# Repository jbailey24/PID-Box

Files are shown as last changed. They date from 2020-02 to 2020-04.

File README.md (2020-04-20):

# PID BOX
### By Julia and Mekhi

<General description of box with photos>
	
Isometric view of boxPID box side viewPID box running

## Initial Planning
 
Digital sketchSketch

The first thing we did when confronted by this new project, is pull out pencils and paper (well, also iPad and stylus). While our initial sketches stayed fairly close to our final product, there were a few major differences, the most notable of which being the shape change. We found that in the end that having it be a cube was better for optimizing space usage. Another thing we changed was the position of the photointerrupter. Originally we had it level with the motor, but because of the shape change, we placed it below the motor in the final design.

## Schedule

| _Week_ | _Goal_ |
|---|---|
| 11/18-11/22| Make schedule and CAD/code foundation |
| 11/25-11/26 | Make RPM code |
| 12/2-12/6 | Make 3D printed parts in CAD and PID Code|
| 12/9-12/13 | Finish CAD model and RGB code |
| 12/16 | Finalize Code, 3D print motor brackets, and laser cut sides |
| 1/6-1/10 | Assemble box |
| 1/13-1/16 | Add code, test, fix errors, repeat |
| 1/20-1/24 | Add code, test, fix errors, repeat |
| 1/27-1/31 | Add code, test, fix errors, repeat |
| 2/3-2/7 | Finish |

## Materials

* Acrylic
* Screws and nuts
* 3D printer
* Arduino Uno
* Breadboard
* Wires
* 6 AA batteries in battery case
* Solder and soldering iron
* DC Motor
* Photointerrupter
* LCD and backpack
* Toggle switch
* LED
* Potentiometer
* RGB LED
* Standoffs
* Washers

## Steps

* Come up with a rough plan and schedule 
* Design PID box in SolidWorks
* 3D print motor bracket
* Laser cut the sides and wheel
* Assemble box
* Wire box
* Write and upload code
* Test and perfect code
* Done!

## CAD
  
Isometric view of CADView of inside of CAD

For this project, we used SolidWorks as our CAD platform. Making a full digital version of our box really helped lay out how we wanted our box to fit together, before wasting any materials. Because we weren't sure of the exact dimensions of the sides, we assigned equations to the box which made it possible to change the sizes of the walls without convoluting any of the other features. This proved very useful, as we changed the dimensions several times before settling on one that worked. In the end, we found that a perfect cube accommodated the different parts most efficiently. 

## Code

For this project, the code was actually rather simple once you know what to do. The PID code is quite complicated, as it uses several calculus functions, but you don’t need to understand calculus to code it. The biggest task that I had to complete was probably finding a way to code the RPM without using delays. I eventually did this using an additional variable and activating the code only if the time since startup is greater than the variable. The variable was then added to every time the code triggered. The biggest issue was actually just missing a single word of code, which stopped the photointerrupter from triggering properly.
  
###### [Link to Code](https://github.com/jbailey24/PID-Box/blob/master/PID-Box_Final/PID-Box_Final.ino)

## Wiring

###### [Link to Fritzing](https://github.com/jbailey24/PID-Box/blob/master/PID_Fritzing.fzz)
Fritzing Diagram
 
## Noteable Components
* RGB LED
  * We thought it would be fun the try our hand at something neither of us had used before. While fairly straightforward, the LED adds an interesting visual to our project. It turns red when the wheel is slower and fades to green as the wheel speeds up. 
* Motor Bracket
  * The motor bracket, inspired by the motor brackets used by the BACON FTC team, consists of two halves, which clamp the motor between them using screws. This allows for a better grip on the motor, which is essential for a more stable wheel. 
* Battery Mount
  * We wanted the battery case to mainly sit inside the box, with only the front sticking out. We drilled two holes in the top of the case so we could screw it to the wall. To prevent it from being pushed inwards on the bottom, we added two groves to the hole in the acrylic that fit the groves on the battery case.

## Encountered Issues

* Warped wheel
  * Problem - The wheel was warped so much that it was unable to turn in the slot.
  * Solution - We recut the slot in the acrylic to be wider and worked on adjusting the wheel so it would spin more fluidly.
* LCD
  * Problem - The LCD had trouble staying on. It would flicker and dim when any tension was put on it.
  * Solution - At first we thought it had something to do with the LCD backpack, but the problem persisted even after we replaced it. We replaced it again, and this time we replaced the LCD too, which seemed to work.
* Number of data points per rotation
  * Problem - When we originally designed the wheel, we only had one hole it it. This meant we could only get one reading per rotation and that it took two whole rotations to get any output. For a project that needs to be constantly outputting and updating data, that’s a pretty serious flaw. 
  * Solution - We did a quick circular pattern and walk over to the laser cutter, and boom a wheel with 6 holes. The most time consuming part of this process was just attaching the wheel. We had to unwire the motor and photointerruper as well as take off an entire side of the box to get it on.

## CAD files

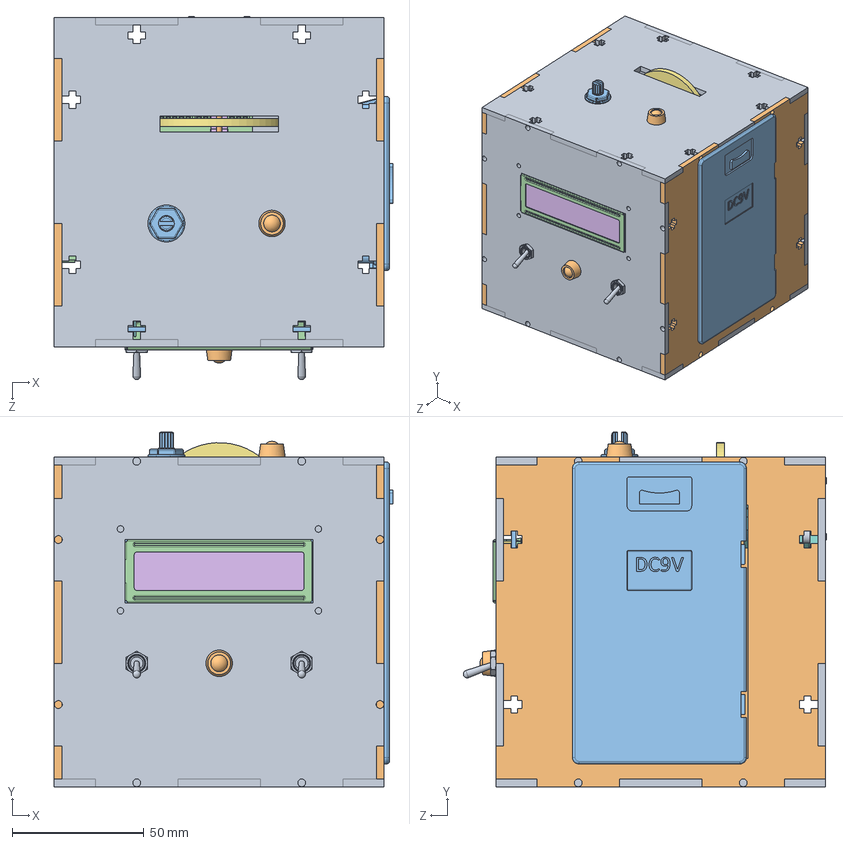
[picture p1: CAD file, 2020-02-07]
MainAssembly.SLDASM
128.2 x 134.5 x 137.7 mm
BiggerWalls x 4
LCD_PCB
metal_casing
LCDbacklight
LCD
conductors x 2
LCD Backpack
Panel Mount SPDT x 2
Panel Mount LED x 2
ArduinoUno
25x.5 Aluminum Hex Female Female Standoff x 4
EE-SX672WR
Wheel
Motorbracket x 2
socket head cap screw_ai x 6
DCmotor-Size130
Panel Mount 10k Potentiometer
Half Breadboard

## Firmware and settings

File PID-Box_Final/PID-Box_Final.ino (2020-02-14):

# include <Wire.h>
# include <LiquidCrystal_I2C.h>
LiquidCrystal_I2C lcd(0x27, 16, 2); //LCD Backpack.ino

volatile int output = 0; //an integer increased in the interrupt
int targetspd = 0; //the set speed of the motor; going to be changed based off of potentiometer value
bool juston = 0; // used for PID initiation sequence timings

const int potentiometer = A1; //the potentiometer pin
const int pinterrupter = 3; //photo interrupter
const int motorpin = 6; // motor
const int wheeled = 13;// LED pin which triggers in the interrupt

const int holenum = 6; // number of holes in the wheel
const int calcps = 3; // how many times the RPM and PID are being calculated in a second
int wt = 1000 / calcps; // wait time; used in PID calculations

int realrpm = 0; // this is the PV, the process variable. Process variable is another name for the actual value of a variable.

long oldmillis = 0; //used for timing instead of delays

const int maxrpmval = 1500;//the supposed max rpm value

const int red = 9;// the three RGB LED pins
const int green = 10;
const int blue = 11;

int error = 0; // both used for Proportional calculations
int previous_error = 0;

int integral = 0; //PID variables
int derivative = 0;
int drive = 0;

double kP = 1.4; //PID tuning variables; note: kI is small because it is divided by 333 for wait time, kD is large because it is multiplied by 333
double kI = 0.004;
double kD = 100;


void setup()
{
  Serial.begin(9600);

  pinMode(pinterrupter, INPUT_PULLUP); //setup for photointerrupter
  pinMode(4, INPUT); //setup for the PID switch
  attachInterrupt(digitalPinToInterrupt(pinterrupter), RPMCalc, RISING);
  pinMode(wheeled, OUTPUT);
  lcd.init();
  lcd.backlight();
  lcd.begin (16, 2); // for 16 x 2 LCD module]
  lcd.setCursor(0, 0);
  lcd.print("Julia Bailey");
  lcd.setCursor(0, 1);
  lcd.print(" Mekhi Hernandez");
  delay(1500);
  lcd.setCursor(0, 0);
  lcd.print("True Speed:      ");
  lcd.setCursor(0, 1);
  lcd.print("Set Speed:       ");
}


void loop()
{

  if (millis() >= oldmillis * wt) //if a certain number(333 currently) of milliseconds have passed since last activation, run this code
  {
    detachInterrupt(digitalPinToInterrupt(pinterrupter)); //detach the interruptss

    targetspd = analogRead(potentiometer);

    realrpm = (output) * (60 * calcps) / holenum; //the RPM is equal to the number of times the photo interrupter has been triggered, times 30. This number is the number of seconds, times the calculations per second, divided by the number of holes

    lcd.setCursor(12, 0); //these 6 lines print the RPM and the set speed
    lcd.print(realrpm);
    lcd.print("   ");
    lcd.setCursor(11, 1);
    lcd.print(map(analogRead(potentiometer), 0, 1023, 0, maxrpmval));
    lcd.print("   ");


    Serial.print(constrain(realrpm, 0, maxrpmval + 1000)); //print the real rpm and the set speed to the serial monitor for graphing
    Serial.print(",");
    Serial.println(map(analogRead(potentiometer), 0, 1023, 0, maxrpmval));

    output = 0; //resets the output value so that we can calculate the next rpm

    if (digitalRead(4) == 1) // if the PID is off, set the adjustment value to 0
    {
      juston = false;
      drive = 0;
    }


    if (digitalRead(4) == 0)
    {

      if (juston == false) //If PID switch is on and it previously wasn't, start initialization sequence
      {
        lcd.clear();
        lcd.setCursor(0, 0);
        lcd.print("PID is on"); //start with this message then wait a second and move to the usual message
        delay(1000);
        lcd.setCursor(0, 0);
        lcd.print("True Speed:      ");
        lcd.setCursor(0, 1);
        lcd.print("Set Speed:       ");
      }

      error = map(targetspd, 0, 1023, 0, 150) - map(realrpm, 0, maxrpmval, 0, 150);//set the error equal to the targetspeed (as a motor usable value) minus the actual rpm mapped as a motor usable value
      integral = integral + (error * wt); // integral is set to the previous integral plus the error
      derivative = (error - previous_error) / wt; // the derivative is the error minus the previous error divided by the amount of time in which it gets calculated
      drive = (error * kP) + (integral * kI) + (derivative * kD); // all of the different adjusting mechanisms are combined
      previous_error = error;

      juston = true;
    }
    analogWrite(motorpin, constrain((map(targetspd, 0, 1023, 0, 150) + drive), 0, 255)); //write to the motor the potentiometer value plus PID stuff
    oldmillis = oldmillis + (1);
    attachInterrupt(digitalPinToInterrupt(pinterrupter), RPMCalc, RISING);
  }


  analogWrite(red, (150 - (map(constrain(realrpm, 0, 1500), 0, maxrpmval, 0, 150)))); // if rpm is zero, light is green; if rpm is maxed, no green
  analogWrite(green, map(constrain(realrpm, 0, 1500), 0, maxrpmval, 0, 150));// print to the green part of the RGBLED the speed of the motor


}

void RPMCalc() // the code to count the number of times the wheel has passed the photo interrupter and to switch the led on momentarily
{

  output ++;
  digitalWrite(wheeled, HIGH);
  delay(1);
  digitalWrite(wheeled, LOW);
}

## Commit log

2020-02-07 Adding Files
    [MainAssembly.SLDASM]
2020-02-10 Adding Fritzing
    [PID_Fritzing.fzz]
2020-02-10 Adding Materials to README
